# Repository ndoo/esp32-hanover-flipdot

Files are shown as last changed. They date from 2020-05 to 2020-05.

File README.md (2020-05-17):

# ESP32 Hanover Flip-dot Sign Controller

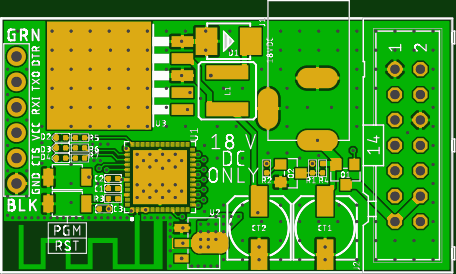
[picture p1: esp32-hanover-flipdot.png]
PCB Top Render


This controller directly controls Hanover Displays Ltd. dot-boards CMOS logic hardware directly through the parallel 14-pin ribbon cable, without the Hanover 7070 or 7080 processor board.

## Design Considerations

This controller's design is based on [Damien Walsh's work on Hanover flip-dot signs](https://damow.net/fun-with-flip-dot-displays/), with only layout changes targeting PCB fabrication and assembly services.

The following considerations went into the PCB schematic and layout:

* SMT components used where possible
* All components are only on the top side of the PCB
* The ESP32-PICO-D4 SIP is used instead of a separate ESP32 module
* PCB size minimized to increase savings with panelization
* All board enable lines are connected to support up to 4 parallel dot-boards
* Generous use of ground stitching vias

## PCBA Notes

### Time/Money Saving

I strongly suggest removing the following items from the PCBA BoM, as they are generic 2.54mm through-hole parts and can be easily sourced at a local dealer:

* J2: CONN HEADER R/A 14POS 2.54MM
* J3: DIP Black Male Header VERT

### Dot-board Ribbon Cable

J2 is specified as a 2x7 pin 2.54mm pitch shrouded header for IDC cables, so a matching 2x7 pin 2.54mm pitch IDC connector must be retrofitted on the original Hanover dot-board ribbon cable.

The original Hanover cable is a Lumberg Micromodul series MICA 14 connector which mates to a corresponding MICS 14 header. As the Lumberg Micromodul parts are much harder to source (with the bottom line being that they cost more) and requires a custom footprint on the PCB, a jellybean part solution was preferred.

### Bill of Materials

The BOM CSV provided uses [Seeed Studio OPL](https://www.seeedstudio.com/opl.html) SKUs for jellybean parts as I have a personal preference for Seeed Studio's Fusion PCBA service. If using other PCBA services, please substitute the Seeed OPL SKUs accordingly.

## Firmware

Reference ESP32 Arduino framework firmware source is available at [ndoo/esp32-hanover-flipdot-firmware](https://github.com/ndoo/esp32-hanover-flipdot-firmware)

### ESP32 GPIO mapping

* Enable Display 1 - GPIO 15
* Enable Display 2 - GPIO 13
* Enable Display 3 - GPIO 12
* Enable Display 4 - GPIO 14
* Column Advance - GPIO 27
* Reset - GPIO 26
* Set/Unset - GPIO 25
* Row Advance - GPIO 33
* Coil Pulse - GPIO 2
* LED 1 - GPIO 23
* LED 2 - GPIO 19
* LED 3 - GPIO 22

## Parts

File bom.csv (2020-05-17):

Designator | Manufacturer Part Number | Quantity
C1 | 302010003 | 1
C2 | 302010053 | 1
C3 | 302010024 | 1
CT1 | 302030000 | 1
CT2 | 302030053 | 1
D1 | 304020021 | 1
D2,D3,D4 | 304090016 | 3
J1 | 320120003 | 1
J2 | 30314-6002HB | 1
J3 | 320020078 | 1
L1 | 303010155 | 1
Q1 | 305030010 | 1
Q2 | 305010018 | 1
R1,R2 | 301010028 | 2
R5,R6,R7 | 301010549 | 3
R3,R4 | 301010047 | 2
RST,PGM | 311020740 | 2
U1 | ESP32-PICO-D4 | 1
U2 | 310030095 | 1
U3 | LM2576SX-5.0/NOPB | 1

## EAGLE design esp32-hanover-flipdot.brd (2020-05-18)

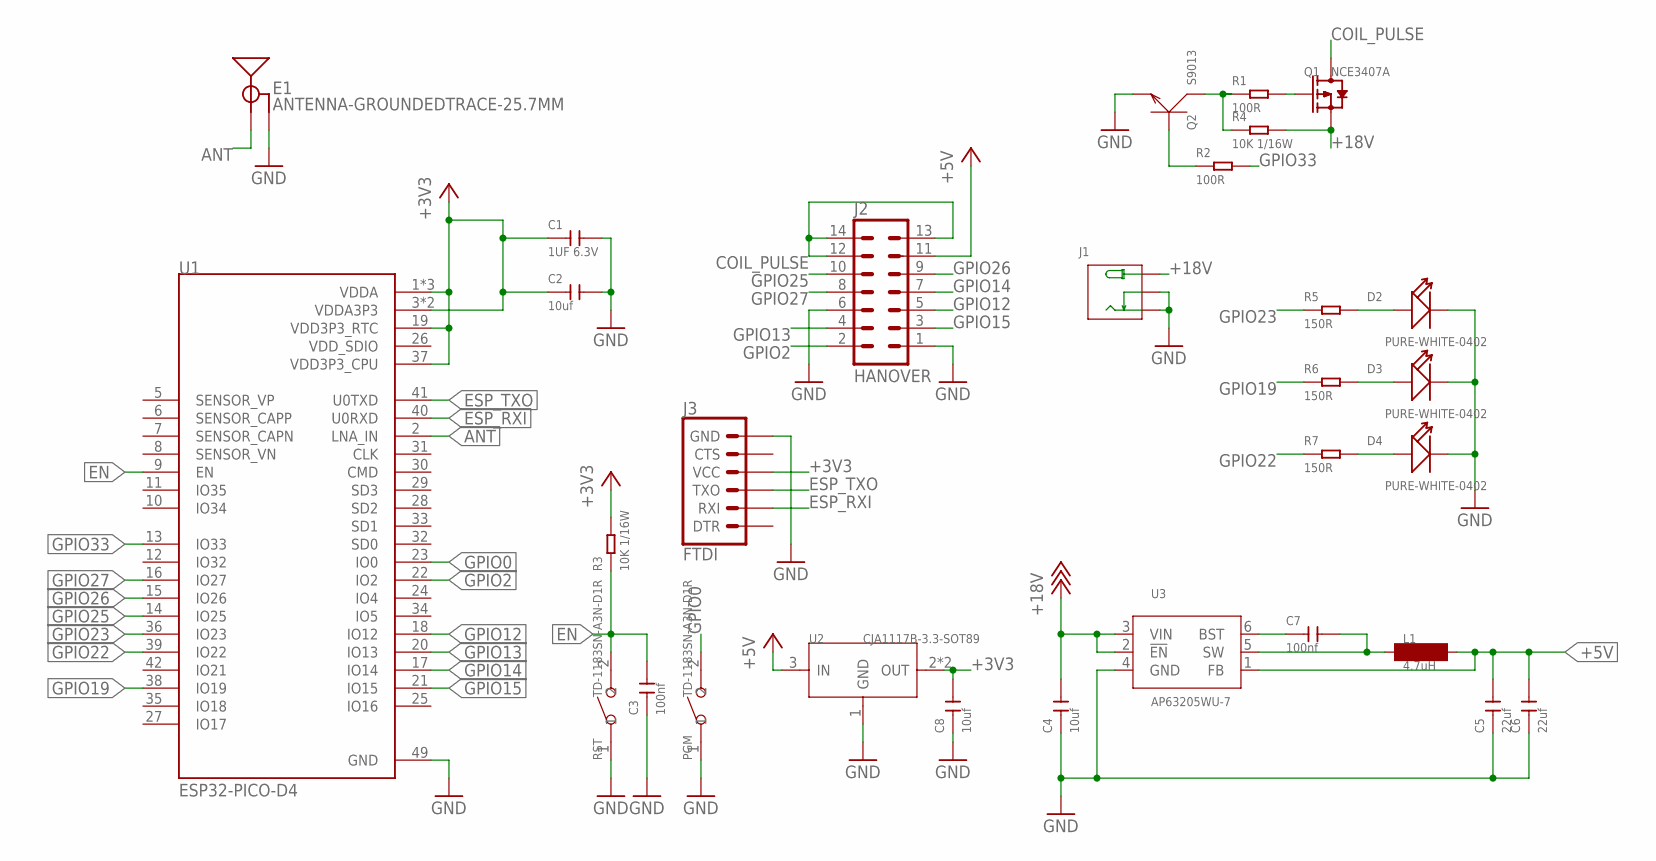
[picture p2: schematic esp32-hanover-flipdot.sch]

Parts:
C1: 1UF 6.3V; C0402
C2, C8: 10uf; C0402
C3, C7: 100nf; C0402
C4: 10uf; C0805
C5, C6: 22uf; C0805
D2, D3, D4: PURE-WHITE-0402; LED-0402
E1: ANTENNA-GROUNDEDTRACE-25.7MM; TRACE_ANTENNA_2.4GHZ_25.7MM
J1: DC-005; 3P-L14.2*W11.0*H9.0MM
J2: HANOVER; ML14
J3: FTDI; 6_PIN_SERIAL_TARGET_SIDE_W_SILK
L1: 4.7uH; INDC2016X100N
PGM: TD-1183SN-A3N-D1R; SW2-2.6-3.0X2.5X1.2+0.4MM
Q1: NCE3407A; SOT-23
Q2: S9013; SOT-23
R1, R2: 100R; R0402
R3, R4: 10K 1/16W; R0402
R5, R6, R7: 150R; R0402; MPN RC0402FR-07150RL
RST: TD-1183SN-A3N-D1R; SW2-2.6-3.0X2.5X1.2+0.4MM
U1: ESP32-PICO-D4; PQFN50P700X700X104-49N
U2: CJA1117B-3.3-SOT89; SOT-89
U3: AP63205WU-7; SOT95P280X100-6N

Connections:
+3V3: C1.1, C2.1, C8.2, J3.P$4 (VCC), R3.2, U1.1 (VDDA), U1.3 (VDDA3P3), U1.4 (VDDA3P3), U1.19 (VDD3P3_RTC), U1.37 (VDD3P3_CPU), U1.43 (VDDA), U1.46 (VDDA), U2.2 (OUT), U2.4 (OUT)
+5V: C5.2, C6.2, J2.11, L1.2, U2.3 (IN), U3.1 (FB)
+18V: C4.2, J1.+B (+), J1.+T (+), Q1.2 (S), R4.2, U3.2 (!EN), U3.3 (VIN)
ANT: E1.ANT (SIGNAL), U1.2 (LNA_IN)
COIL_PULSE: J2.12, J2.13, J2.14, Q1.3 (D)
EN: C3.2, R3.1, RST.2, U1.9 (EN)
ESP_RXI: J3.P$3 (RXI), U1.40 (U0RXD)
ESP_TXO: J3.P$2 (TXO), U1.41 (U0TXD)
GND: C1.2, C2.2, C3.1, C4.1, C5.1, C6.1, C8.1, D2.-, D3.-, D4.-, E1.GND, E1.GND2 (GND), J1.-1B (-), J1.-1T (-), J1.-2B (CDN), J1.-2T (CDN), J2.1, J2.6, J3.P$6 (GND), PGM.1, Q2.2 (E), RST.1, U1.49 (GND), U2.1 (GND), U3.4 (GND)
GPIO0: PGM.2, U1.23 (IO0)
GPIO2: J2.2, U1.22 (IO2)
GPIO12: J2.5, U1.18 (IO12)
GPIO13: J2.4, U1.20 (IO13)
GPIO14: J2.7, U1.17 (IO14)
GPIO15: J2.3, U1.21 (IO15)
GPIO19: R6.1, U1.38 (IO19)
GPIO22: R7.1, U1.39 (IO22)
GPIO23: R5.1, U1.36 (IO23)
GPIO25: J2.10, U1.14 (IO25)
GPIO26: J2.9, U1.15 (IO26)
GPIO27: J2.8, U1.16 (IO27)
GPIO33: R2.2, U1.13 (IO33)
unnamed: Q1.1 (G), R1.2
unnamed: Q2.3 (C), R1.1, R4.1
unnamed: Q2.1 (B), R2.1
unnamed: C7.1, U3.6 (BST)
unnamed: D2.+, R5.2
unnamed: D3.+, R6.2
unnamed: D4.+, R7.2
unnamed: C7.2, L1.1, U3.5 (SW)
VDD_SDIO: U1.26 (VDD_SDIO)

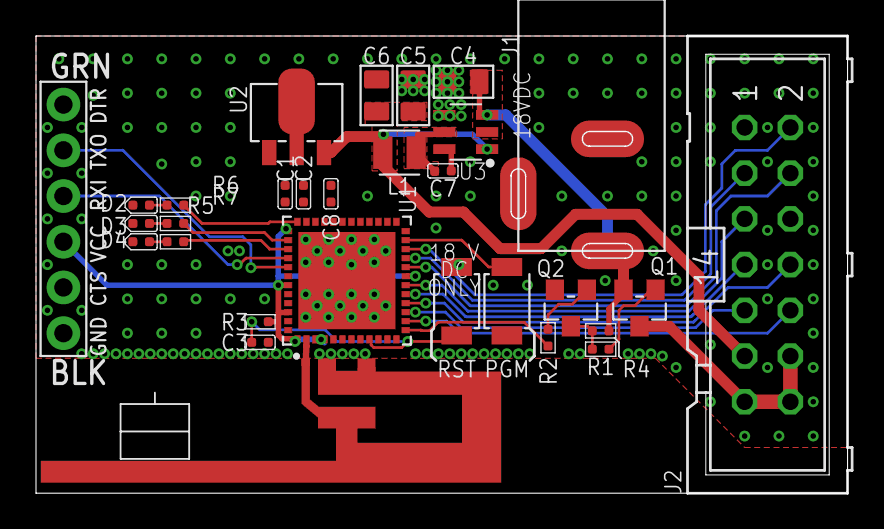
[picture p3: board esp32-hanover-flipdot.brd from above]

Board: 2 copper layers, 45.1 x 25.4 mm, 30 parts (0 on the bottom side), 30 nets.

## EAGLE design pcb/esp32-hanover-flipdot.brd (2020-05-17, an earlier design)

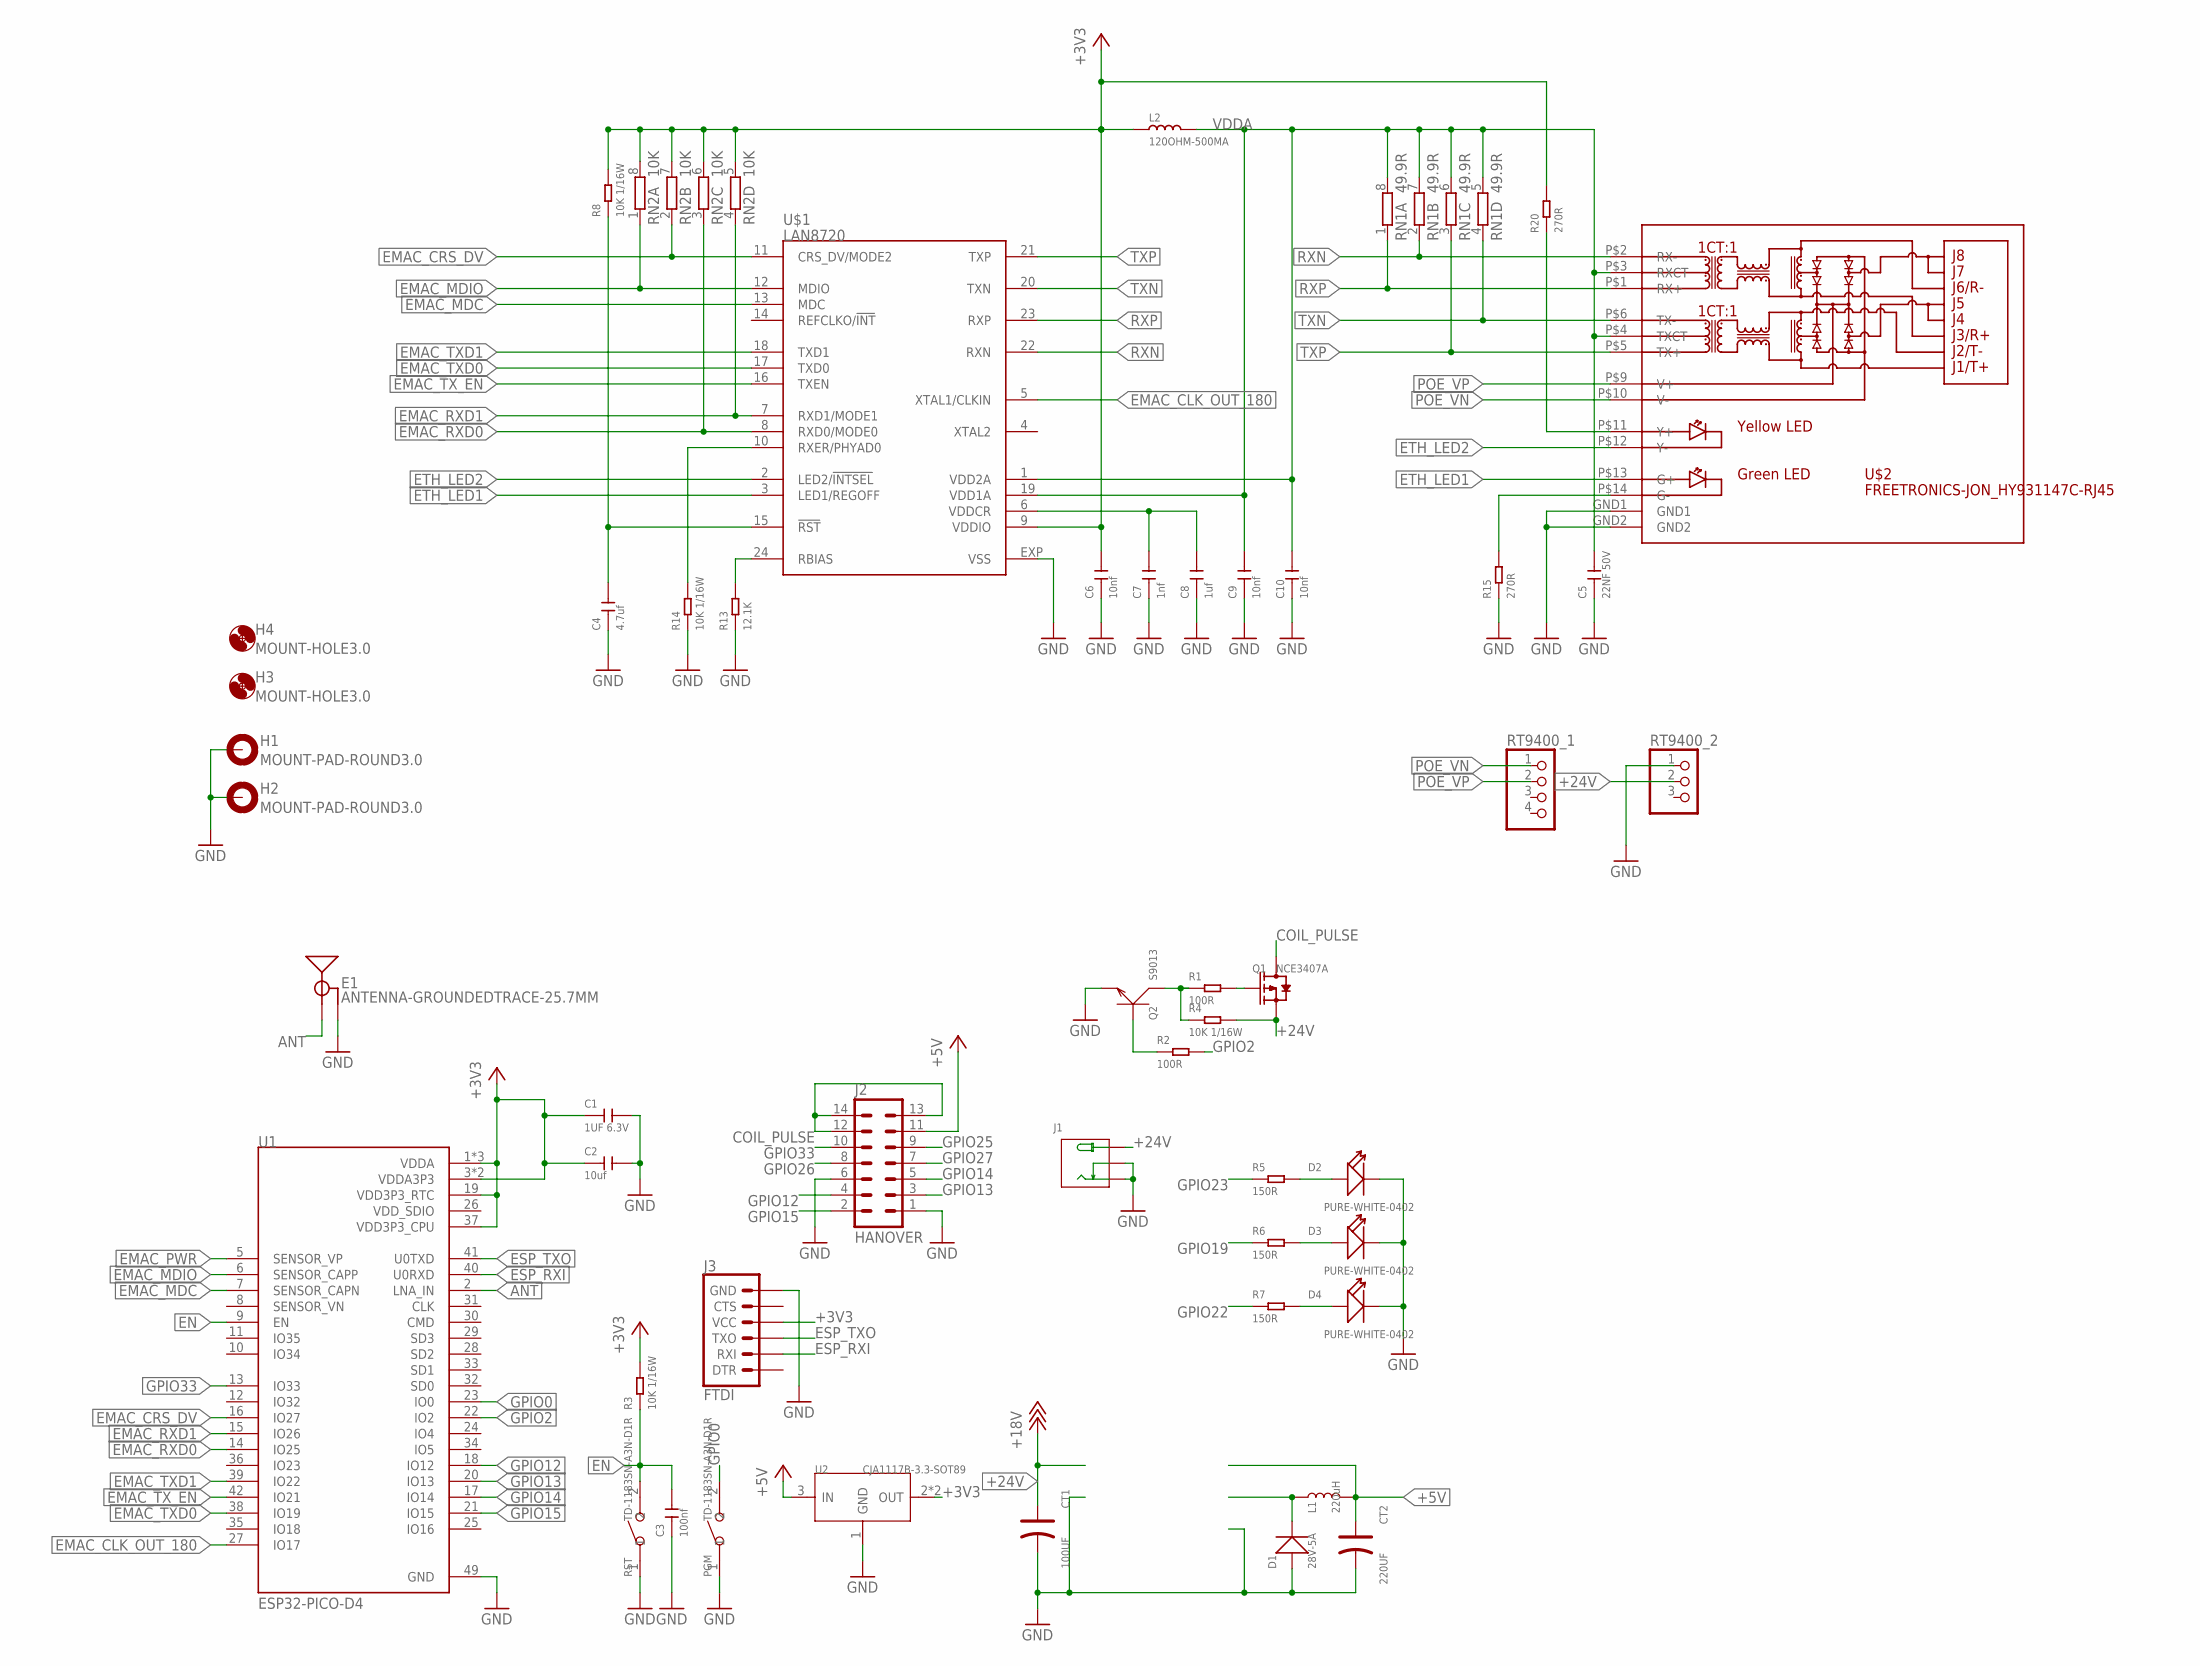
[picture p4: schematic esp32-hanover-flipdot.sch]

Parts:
C1: 1UF 6.3V; C0402
C2: 10uf; C0402
C3: 100nf; C0402
C4: 4.7uf; C0402
C5: 22NF 50V; C0402
C6, C9, C10: 10nf; C0402
C7: 1nf; C0402
C8: 1uf; C0402
CT1: 100UF; ELECTRO-SMD-C-6MM; MPN 302030000
CT2: 220UF; ELECTRO-SMD-C-6MM
D1: 28V-5A; DO-214AA
D2, D3, D4: PURE-WHITE-0402; LED-0402
E1: ANTENNA-GROUNDEDTRACE-25.7MM; TRACE_ANTENNA_2.4GHZ_25.7MM
H1, H2: MOUNT-PAD-ROUND3.0; 3,0-PAD
H3, H4: MOUNT-HOLE3.0; 3,0
J1: DC-005; 3P-L14.2*W11.0*H9.0MM
J2: HANOVER; ML14
J3: FTDI; 6_PIN_SERIAL_TARGET_SIDE_W_SILK
L1: 220uH; CR54
L2: 120OHM-500MA; L0603
PGM: TD-1183SN-A3N-D1R; SW2-2.6-3.0X2.5X1.2+0.4MM
Q1: NCE3407A; SOT-23
Q2: S9013; SOT-23
R1, R2: 100R; R0402
R3, R4, R8, R14: 10K 1/16W; R0402
R5, R6, R7: 150R; R0402; MPN RC0402FR-07150RL
R13: 12.1K; R0402
R15, R20: 270R; R0402
RN1: 49.9R; YC124; MPN YC124-FR-0749R9L
RN2: 10K; YC124; MPN YC124-FR-0710KL
RST: TD-1183SN-A3N-D1R; SW2-2.6-3.0X2.5X1.2+0.4MM
RT9400_1: PINHD-1X4; 1X04
RT9400_2: PINHD-1X3; 1X03
U1: ESP32-PICO-D4; PQFN50P700X700X104-49N
U2: CJA1117B-3.3-SOT89; SOT-89
U$1: LAN8720; QFN24
U$2: FREETRONICS-JON_HY931147C-RJ45; FREETRONICS-JON_HY931147C

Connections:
+3V3: C1.1, C2.1, C6.2, J3.P$4 (VCC), L2.1, R3.2, R8.2, R20.2, RN2.5 (2), RN2.6 (2), RN2.7 (2), RN2.8 (2), U1.1 (VDDA), U1.3 (VDDA3P3), U1.4 (VDDA3P3), U1.19 (VDD3P3_RTC), U1.37 (VDD3P3_CPU), U1.43 (VDDA), U1.46 (VDDA), U2.2 (OUT), U2.4 (OUT), U$1.9 (VDDIO)
+5V: CT2.+, J2.11, L1.P$2 (2), U2.3 (IN)
+24V: CT1.+, J1.+B (+), J1.+T (+), Q1.2 (S), R4.2, RT9400_2.2
ANT: E1.ANT (SIGNAL), U1.2 (LNA_IN)
COIL_PULSE: J2.12, J2.13, J2.14, Q1.3 (D)
EMAC_CLK_OUT_180: U1.27 (IO17), U$1.5 (XTAL1/CLKIN)
EMAC_CRS_DV: RN2.2 (1), U1.16 (IO27), U$1.11 (CRS_DV/MODE2)
EMAC_MDC: U1.7 (SENSOR_CAPN), U$1.13 (MDC)
EMAC_MDIO: RN2.1, U1.6 (SENSOR_CAPP), U$1.12 (MDIO)
EMAC_PWR: U1.5 (SENSOR_VP)
EMAC_RXD0: RN2.3 (1), U1.14 (IO25), U$1.8 (RXD0/MODE0)
EMAC_RXD1: RN2.4 (1), U1.15 (IO26), U$1.7 (RXD1/MODE1)
EMAC_TXD0: U1.38 (IO19), U$1.17 (TXD0)
EMAC_TXD1: U1.39 (IO22), U$1.18 (TXD1)
EMAC_TX_EN: U1.42 (IO21), U$1.16 (TXEN)
EN: C3.2, R3.1, RST.2, U1.9 (EN)
ESP_RXI: J3.P$3 (RXI), U1.40 (U0RXD)
ESP_TXO: J3.P$2 (TXO), U1.41 (U0TXD)
ETH_LED1: U$1.3 (LED1/REGOFF), U$2.P$13 (G+)
ETH_LED2: U$1.2 (LED2/!INTSEL), U$2.P$12 (Y-)
GND: C1.2, C2.2, C3.1, C4.1, C5.1, C6.1, C7.1, C8.1, C9.1, C10.1, CT1.-, CT2.-, D1.+, D2.-, D3.-, D4.-, E1.GND, E1.GND2 (GND), H1.B3,0, H2.B3,0, J1.-1B (-), J1.-1T (-), J1.-2B (CDN), J1.-2T (CDN), J2.1, J2.6, J3.P$6 (GND), PGM.1, Q2.2 (E), R13.1, R14.1, R15.1, RST.1, RT9400_2.1, U1.49 (GND), U2.1 (GND), U$1.EXP (VSS), U$2.GND1, U$2.GND2
GPIO0: PGM.2, U1.23 (IO0)
GPIO2: R2.2, U1.22 (IO2)
GPIO12: J2.4, U1.18 (IO12)
GPIO13: J2.3, U1.20 (IO13)
GPIO14: J2.5, U1.17 (IO14)
GPIO15: J2.2, U1.21 (IO15)
GPIO19: R6.1
GPIO22: R7.1
GPIO23: R5.1
GPIO25: J2.9
GPIO26: J2.8
GPIO27: J2.7
GPIO33: J2.10, U1.13 (IO33)
unnamed: Q1.1 (G), R1.2
unnamed: Q2.3 (C), R1.1, R4.1
unnamed: Q2.1 (B), R2.1
unnamed: D1.-, L1.P$1 (1)
unnamed: D2.+, R5.2
unnamed: D3.+, R6.2
unnamed: D4.+, R7.2
unnamed: R14.2, U$1.10 (RXER/PHYAD0)
unnamed: R13.2, U$1.24 (RBIAS)
unnamed: R15.2, U$2.P$14 (G-)
unnamed: C7.2, C8.2, U$1.6 (VDDCR)
unnamed: R20.1, U$2.P$11 (Y+)
unnamed: C4.2, R8.1, U$1.15 (!RST)
POE_VN: RT9400_1.1, U$2.P$10 (V-)
POE_VP: RT9400_1.2, U$2.P$9 (V+)
RXN: RN1.2 (1), U$1.22 (RXN), U$2.P$2 (RX-)
RXP: RN1.1, U$1.23 (RXP), U$2.P$1 (RX+)
TXN: RN1.4 (1), U$1.20 (TXN), U$2.P$6 (TX-)
TXP: RN1.3 (1), U$1.21 (TXP), U$2.P$5 (TX+)
VDDA: C5.2, C9.2, C10.2, L2.2, RN1.5 (2), RN1.6 (2), RN1.7 (2), RN1.8 (2), U$1.1 (VDD2A), U$1.19 (VDD1A), U$2.P$3 (RXCT), U$2.P$4 (TXCT)
VDD_SDIO: U1.26 (VDD_SDIO)

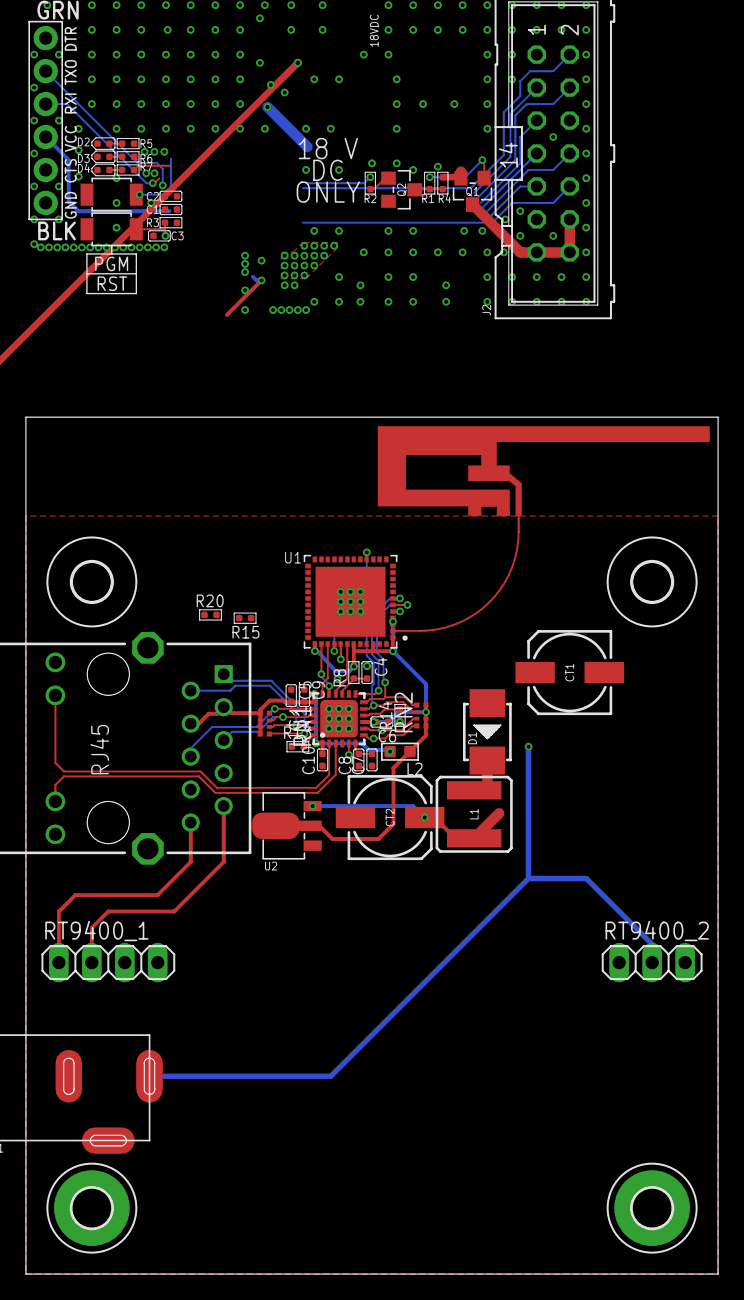
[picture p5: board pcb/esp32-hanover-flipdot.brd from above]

Board: 2 copper layers, 53.3 x 66.0 mm, 50 parts (0 on the bottom side), 47 nets.

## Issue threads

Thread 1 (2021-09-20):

Update jellybean SKUs

briggySmalls, 2021-09-20:
Hi @ndoo 👋

Now I find myself on _your_ repo. I'm super interested in this project! I'd love to up the refresh rate of my signs by bypassing the old control boards. Your work here seems really thorough too!

I'm not very familiar with PCBA. I've downloaded Eagle and attempted to plug this BOM into a local (UK) PCBA company (https://www.pcbtrain.co.uk). However I notice that the majority of the parts in the BOM are no longer found, even on SeeedStudio's website using the OPL you linked (https://www.seeedstudio.com/opl.html).

Could I ask what the process would be for updating this BOM with relevant parts? I'd really like to get hold of one of these controllers 🙏

juliango202, 2021-12-18:
Hello guys,
I too have acquired an Hanover display to hack around and would be super interested to build this controller! Any website where we can source the parts? @briggySmalls could you make any progress here?

sam-briggs-depop, 2021-12-18:
I haven’t sadly. I got as far as above really. Although I had more luck using octopart. I’m not really electronics literate so I’m unsure how to identify drop in replacements even for jellybean parts.
I keep meaning to come back to this and start taking a punt on replacements.
Or maybe the answer is to pay someone on upwork 🤔

juliango202, 2021-12-19:
OK understood thanks! I'm also not an electronics person myself, I can solder some components to a board but that's about it ;)  I'm into this for the programming / artsy possibilities, but it would be great to profit from Andrew's work to improve the refresh rate...
I'm thinking to bring this problem to the local Fablab when I have the chance(January?) and see if I can get some help... If I can come up with a working version I'll post an update here.

chunkysteveo, 2021-12-20:
Don't forget Damien's board are available too and use mostly through-hole components - https://github.com/themainframe/esp32-flipdot-controller/tree/master/pcb

His board only allows for one display to be connected though unless you bodge the enable wires between the connector and ESP32 pins, and the boot pins are floating currently, so would need a bodge fix too.

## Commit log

2020-05-17 pcb: Add Ethernet and PoE
    [esp32-hanover-flipdot.brd, esp32-hanover-flipdot.sch]
2020-05-17 Clean up non-PCB files to be migrated to a fork of the repository
    [bom.csv, esp32-hanover-flipdot.brd, esp32-hanover-flipdot.sch]
2020-05-18 Change buck converter from LM7576-5.0 to AP63205, change antenna
    Change buck converter from LM7576-5.0 to AP63205, which uses drastically less space and switches at a higher frequency thus requiring smaller passives, and does not require a schottky diode.
    Change antenna to a larger inverted-F antenna which has more isotropic gain thus makes placement of the board less of a factor in Wi-Fi performance.
    [esp32-hanover-flipdot.brd, esp32-hanover-flipdot.sch]

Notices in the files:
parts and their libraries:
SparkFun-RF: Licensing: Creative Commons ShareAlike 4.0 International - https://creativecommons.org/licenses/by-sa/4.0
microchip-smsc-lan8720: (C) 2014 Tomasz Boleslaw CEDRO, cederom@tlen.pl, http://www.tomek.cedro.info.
